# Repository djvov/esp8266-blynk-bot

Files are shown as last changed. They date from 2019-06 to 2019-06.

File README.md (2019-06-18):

# ESP8266 and BLYNK 4WD Robot

- [ESP8266 and BLYNK 4WD Robot](#esp8266-and-blynk-4wd-robot)
  * [PINOUT](#pinout)
  * [First firmware update of ESP8266](#first-firmware-update-of-esp8266)
  * [ESP8266 to breadboard](#esp8266-to-breadboard)
  * [Full Schema](#full-schema)
  * [POWER](#power)
  * [MOTOR](#motor)
  * [CONNECTION](#connection)
  * [BLYNK APP](#blynk-app)
  * [Includes](#includes)
  * [Robot settings (variable declaration)](#robot-settings)
  * [Void Setup](#void-setup)
  * [Void Loop](#void-loop)
  * [Functions](#functions)
    + [Strobo function](#strobo-function)
    + [Checkrasst function](#checkrasst-function)
    + [distanceMeasuringSonar function](#distancemeasuringsonar-function)
    + [Movement functions](#movement-functions)

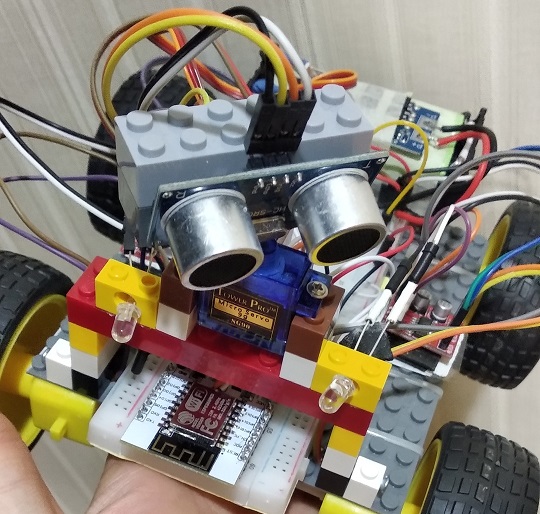
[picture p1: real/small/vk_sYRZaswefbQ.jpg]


[https://github.com/djvov/esp8266-blynk-bot/blob/master/real/vk_sYRZaswefbQ.jpg?raw=true]

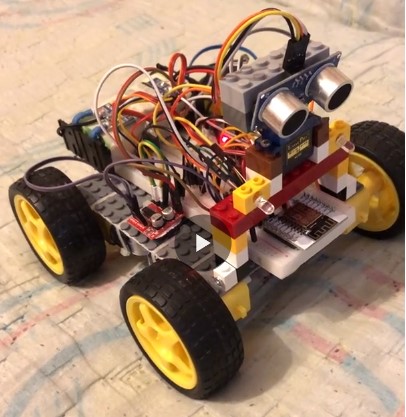
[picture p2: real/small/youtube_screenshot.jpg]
Watch the video (https://www.youtube.com/watch?v=UbAJtE57SPo)


[Table of contents](#esp8266-and-blynk-4wd-robot)

## PINOUT

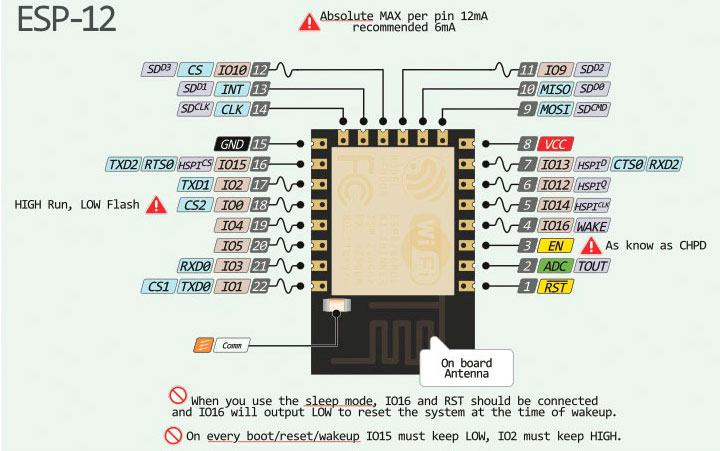
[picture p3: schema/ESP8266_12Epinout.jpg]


[Table of contents](#esp8266-and-blynk-4wd-robot)

## First firmware update of ESP8266

In Arduino IDE setup you need to put "http://arduino.esp8266.com/stable/package_esp8266com_index.json" at the line "Extend links to board manager".
Then go to the Board Manager and install ESP8266 community.
In the board menu choose your chip, my is Generic 8266.
Then your need to put esp8266 and FTDI programmator together as shown below.

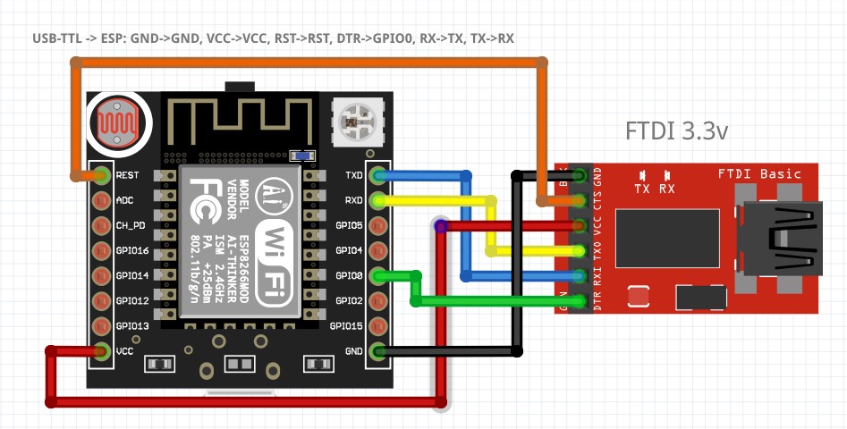
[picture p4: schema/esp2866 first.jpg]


Open Arduino OTA sketch from examples and write it.

Because in this robot I took all PINs to some tasks, we need to write firmware Over The Air. And first step is load OTA firmware to esp8266.

[Table of contents](#esp8266-and-blynk-4wd-robot)

## ESP8266 to breadboard

I'll buy native esp8266 chip and white development board.

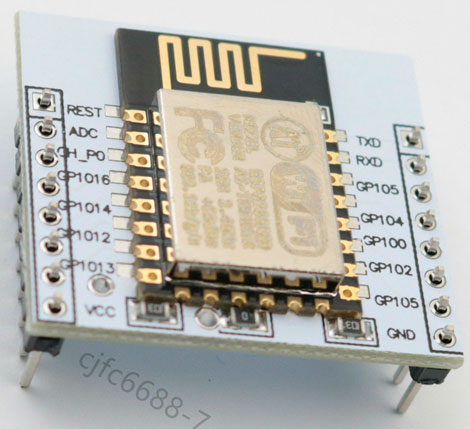
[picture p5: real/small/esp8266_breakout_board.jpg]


In the Fritzing schema I didn't find white pcb, so I put what I found, some black.
But, as white pcb, It's has some width as breadboard width. So we need to extend it by wire to another row. From 1 row to 9 row, from 2 row to 10 row, etc.

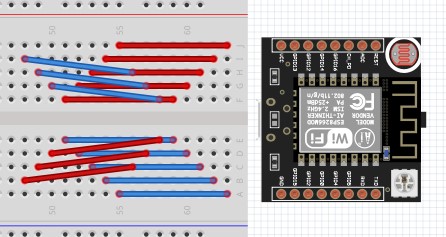
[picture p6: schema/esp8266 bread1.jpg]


The yellow lines just to show hot to each  pin goes to its row after pcb.

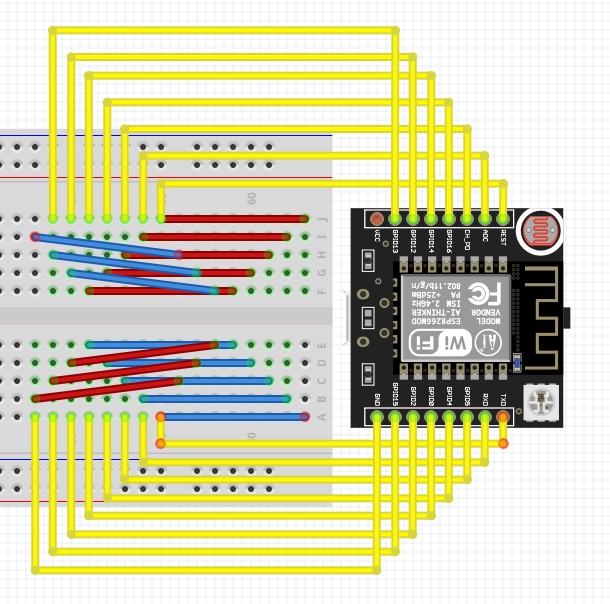
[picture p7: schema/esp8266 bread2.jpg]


[Table of contents](#esp8266-and-blynk-4wd-robot)

## Full Schema

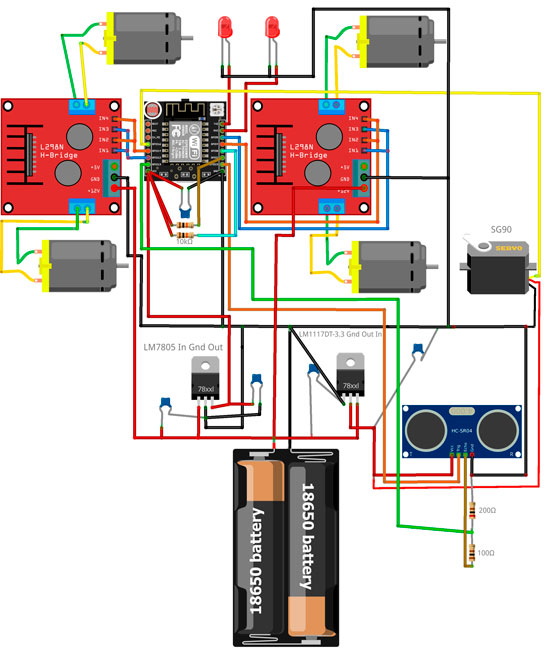
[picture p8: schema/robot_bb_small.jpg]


[https://github.com/djvov/esp8266-blynk-bot/blob/master/schema/robot_bb.jpg?raw=true]

[Table of contents](#esp8266-and-blynk-4wd-robot)

## POWER

First of all, two 18650 with serial connection to get 8.4v. With BMS plate to prevent overdischarge, and charge it with balance.
From battery block we need to build TWO special power lines: 3.3v for ESP8266, 5v for servo and HC–SR04 sonar. And raw 8.4v power for motor drivers.
3.3v we get from LM1117DT-3.3, 5v we get from LM7805. In both case two ceramic 104 capacitor for IN and OUT to ground.
**IMPORTANT!** It is necessary to connect **ALL GROUNDS**

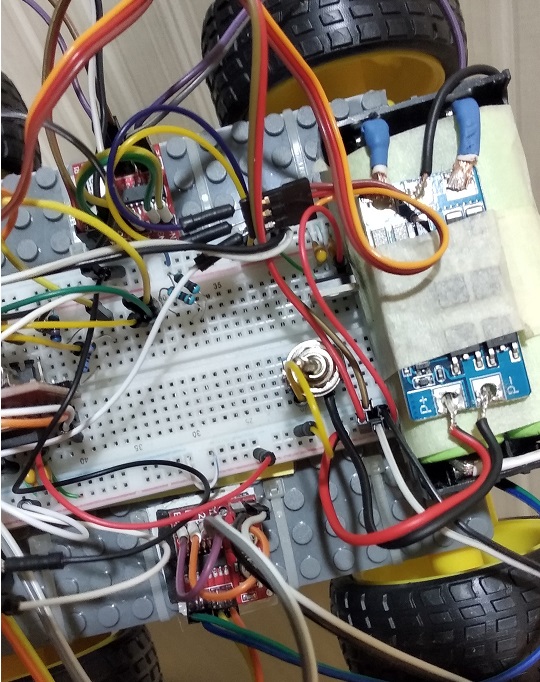
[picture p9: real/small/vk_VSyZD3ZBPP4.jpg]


[Table of contents](#esp8266-and-blynk-4wd-robot)

## MOTOR

I use MX1508 dual motors driver, analog of L298N. 1.5A per channel, 2.5A peak. With no heat sink. Becarefurl with VCC **+** and **-**.

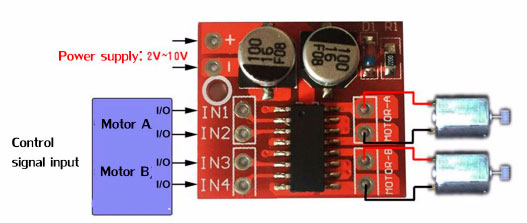
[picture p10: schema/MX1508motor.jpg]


I use two MX1508 dual motors drivers, becase  I have four wheels. One MX1508 drives two motors from same side. So we need to put IN1 and IN3 together, also IN2 and IN4, for same direction of two motors. This schema can use only two pins of ESP8266 instead of four pins.

Here is table of signal for direction, standby and brakes. Standby different from brake. Standby ends of power to motor, and motor stops by itself, it tooks some time. Brake stops motor immediately.

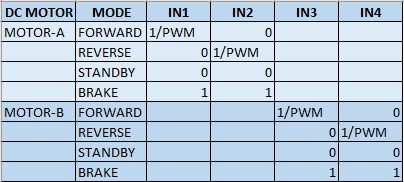
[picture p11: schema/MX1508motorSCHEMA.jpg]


[Table of contents](#esp8266-and-blynk-4wd-robot)

## CONNECTION

White board for ESP8266 already has pull-up 10k resistors for CH_PD and RESET, and pull-down 10k resistor for GPIO15. If you use native ESP8622 chip you must use put this resistor manually. Also, we has to pull-up GPIO2 and GPIO0 with 10k resistors. And I put ceramic 104 capacitor between VCC and GND of ESP8266.

```c
//motors
// left
const int in1 = 12;
const int in2 = 14;
// right
const int in3 = 5;
const int in4 = 4;
```
HC–SR04 sonar use 5v power and 5v TTL logic. But it know about 3.3v TTL for **TRIG** pin (HC–SR04 input). **BUT ECHO** pin (HC–SR04 output) needs to be connect to ESP8266 through voltage divider

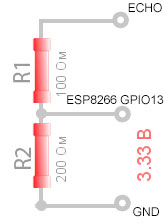
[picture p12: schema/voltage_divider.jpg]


```c
// HC–SR04 sonar
const int trigPin = 15;
const int echoPin = 13; // through voltage divider!
```
LED uses TX and RX pins. THATS WHY FIRST OF ALL WE FLSAH OTA sketch.

```c
// LED
const int led = 1;
const int led1 = 3;
```

Servo SG90 use 5v power and 5v TTL logic. But it know about 3.3v TTL for SG90 input.

```c
//servo
Servo servo1;
const int servoPin = 16;
```

[Table of contents](#esp8266-and-blynk-4wd-robot)

## BLYNK APP

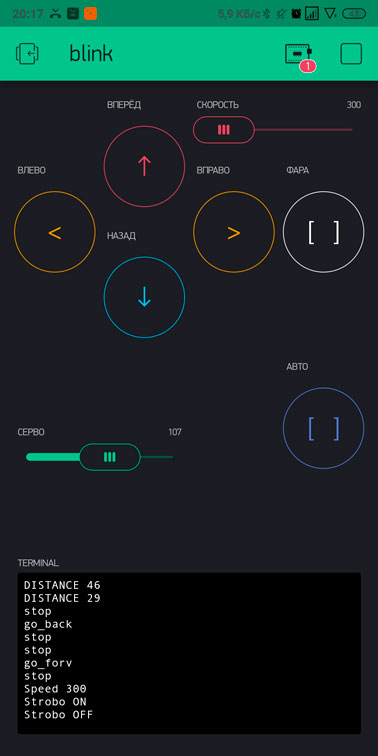
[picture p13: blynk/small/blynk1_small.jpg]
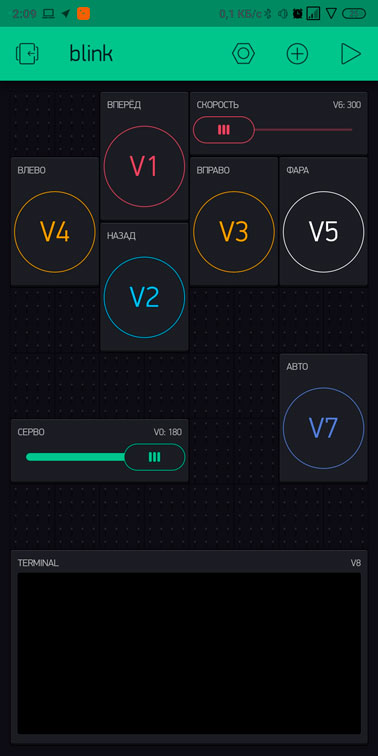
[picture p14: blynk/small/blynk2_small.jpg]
 

```
V0  slider, 0-180, decimals 0, send on release Off. Servo. Just for fun.
    In time the robot walks - servo is worked automatic.
V1-V4 push type buttons, Forward, Revers, Right, Left.
V5  switch type button. LEDs.
V6  slider, 300-600, decimals 0, send on release On. Speed.
V7  switch type button. Automatic walk.
V8  terminal
```

[Table of contents](#esp8266-and-blynk-4wd-robot)

## Includes

For use Blynk App you must need `ESP8266WiFi` and `BlynkSimpleEsp8266` libraries. `ESP8266mDNS` and `WiFiUdp` and `ArduinoOTA` for Over The Air upload. Servo for servo ;-)

```c
#include <ESP8266mDNS.h>
#include <WiFiUdp.h>
#include <ESP8266WiFi.h>
#include <BlynkSimpleEsp8266.h>
#include <ArduinoOTA.h>
#include <Servo.h>
```

[Table of contents](#esp8266-and-blynk-4wd-robot)

## Robot settings

You should get Auth Token in the Blynk App. Get it from Blynk app. And login and password to your router.

```c
// You should get Auth Token in the Blynk App.
char auth[] = "";

// Your WiFi credentials.
char ssid[] = "";
char pass[] = "";
```

Default speed. Slowest 300. If **speed < 300**, motor has not enough power to move. Fastest is 1023. But I set tup fastest is 600 because if **speed > 600**, robot could not stop before it crashes the wall ).

```c
// скорость 1023 max
int spd = 300;
// скорость автопрогулки
int autoSpd = 300;
```

`timerStrob` is for timer that runs stroboscope effect with leds.
`timerStena` is for timer that checks distance to the obstacle in manual mode, it moves the servo to which the sonar is attached.
`timerAuto` is for timer that runs auto walk, it moves the servo to which the sonar is attached.

```c
BlynkTimer timer;
int timerStrob;
int timerStena;
int timerAuto;
```

Movement flags to know where the robot is going.

```c
// флаги движения
int V1_forv = 0;
int V2_back = 0;
int V3_right = 0;
int V4_left = 0;
```

Global variable `autO` that indicates if auto walk running. Last letter is capital because `auto` is reserved word. You may name it `autoWalk`.

```c
// авто прогулка
int autO = 0;
```

Servo angles. In order for the sonar to look forward, the servo must be rotated 90 degrees. Similarly, sonar to right 50 degrees, sonar to left 140 degrees.

```c
// Углы поворота Серовпривода
int angleF = 90;
int angleR = 50;
int angleL = 140;
```

Distances in centimeters. `distAttention` - Speed higher. `distCaution` - Speed lower. `distSTOP` - STOP.

```c
// дистанции остановки
int distSTOP = 30; // дистанция СТОП!
int distCaution = 50; // дистанция ОСТОРОЖНО! скорость 300
int distAttention = 70; // дистанция ВНИМАНИЕ! скорость 400
```

Terminal widget in blynk app attached to Virtual pin 8. For some debug information.

```c
WidgetTerminal terminal(V8);
```

Delay time to stabilize servo.

```c
int delay_time = 150; // время задержки для стабилизации сервопривода
```

[Table of contents](#esp8266-and-blynk-4wd-robot)

## Void Setup

In this section you must initizlize pin mode, attach servo, move it forward (90 degrees), stop motors, turn off the leds.

```c
 // моторы
  pinMode(in1, OUTPUT);
  pinMode(in2, OUTPUT);
  pinMode(in3, OUTPUT);
  pinMode(in4, OUTPUT);
  stp(0);
  // фара leds
  pinMode(led, OUTPUT);
  pinMode(led1, OUTPUT);
  digitalWrite(led, LOW);
  digitalWrite(led1, LOW);
  //датчик расстояния sonar
  pinMode(trigPin, OUTPUT);
  pinMode(echoPin, INPUT);
  // servo
  servo1.attach(servoPin);
  servo1.write(90);
```

Timer setup. BlynkTimer is similar as SimpleTimer. First of all needs to declare timer object in global. `BlynkTimer timer;`
Timer objects can manage several timers. Each of them must be also declared. `int timerStrob;`.
Then we must determine the correspondence between variable and function.
`int setInterval(unsigned long d, timer_callback f);`
First parametr `d` is delay in milliseconds, second parameter `f` is name of callback function that runs every `d` milliseconds.

```c
  timerStrob = timer.setInterval(200, strobo);
```

And disable that timer, because we don't need to all timer functions run at startup.

```c
  timer.disable(timerStrob);
```

We do the same for all timers.

```c
  // увидел ли стену в ручном режиме
  timerStena = timer.setInterval(13L, checkrasst);
  timer.disable(timerStena);

  // автопрогулка
  timerAuto = timer.setInterval(1L, go_auto);
  timer.disable(timerAuto);
```

Then we start OTA and Blynk

```c
// по воздуху
  ArduinoOTA.begin();
  Blynk.begin(auth, ssid, pass);
```

Theb we initilize terminal widget.
`clear` function clear ther terminal. `print` and `println` functions as Serial.print, writes text and return or not return caret.
After we finished all text, we need to terminal sends data to blynk app by the `flush` function.
Lets write some 'hello' text and current IP after robot connects to router.

```c
  terminal.clear();
  terminal.println(String("Speed ") + String(spd));
  terminal.println(String("Servo 90"));
  terminal.print(String("Local IP"));
  terminal.println(WiFi.localIP());
  terminal.flush();
```

[Table of contents](#esp8266-and-blynk-4wd-robot)

## Void Loop

When you use Blynk your **loop section** must contains only `Blynk.run()`. `ArduinoOTA.handle();` if you uses OTA, and `timer.run();` if you uses timer functions. **Thats all!** All loops, cycles, events, actions, etc. in separate functions.

```c
void loop()
{
  ArduinoOTA.handle();
  Blynk.run();
  timer.run();
}
```

[Table of contents](#esp8266-and-blynk-4wd-robot)

## Functions

### Strobo function

Just blink two leds one by one.

```c
void strobo() {
  digitalWrite(led, HIGH);
  digitalWrite(led1, LOW);
  delay(100);
  digitalWrite(led, LOW);
  digitalWrite(led1, HIGH);
}
```

[Table of contents](#esp8266-and-blynk-4wd-robot)

### checkrasst function

Checks distance to the obstacle in manual mode. Servo looks forward (90 degrees). When The robot stop near the 'wall' he shakes his head like a man, means **"NO"**

```c
void checkrasst() { // проверка расстояния в ручном режиме поездки и остановка если мало
  int cm = distanceMeasuringSonar (angleF);
  if (cm<distSTOP) {
    stp(0);
    servo1.write(70);
    delay(500);
    servo1.write(110);
    delay(500);
    servo1.write(90);
  }
}
```

[Table of contents](#esp8266-and-blynk-4wd-robot)

### distanceMeasuringSonar function

Measuring distance to the obstacle at the some angle. `angle` parameter in degrees. In [settings](#robot-settings) we declare some variables for some angles. Turn the servo, wait for stabilization. Then use sonar. If result of the `pulseIn` function is **0** this means error of measurement, and we need to restart sonar by send **low** to `echoPin`, before this turn `echoPin` in **OUTPUT mode**, and back in **INPUT** mode after sonar reset. And I decided return 400cm in this case (limit of measurement). If everything is ok, divide result of the `pulseIn` function by 58, we get distance in **cm**.

```c
// *************** Функция определения Расстояния СОНАР ******************
int distanceMeasuringSonar (int angle)// функция — измерение расстояния при определенном угле поворота сервопривода
{
  int distanceSonar = 0;
  servo1.write(angle); // поворот сервопривода 1
  delay (delay_time); // подождать стабилизацию сервопривода
  digitalWrite (trigPin, LOW); // подать напряжение на сонар LOW в течении 2¦Мs
  delayMicroseconds (2);
  digitalWrite (trigPin, HIGH); // подать напряжение HIGH на сонар в течении 10¦Мs
  delayMicroseconds (10);
  digitalWrite (trigPin, LOW); // подать напряжение LOW на сонар
  int distance = pulseIn(echoPin, HIGH, 30000); // считываем данные с Сонара
  if (distance == 0)// если расстояние "0" — ошибка измерения (вне предела/завис)
  { // делаем перезагрузку сонара подачей 0 на вывод ECHO Сонара
    pinMode(echoPin, OUTPUT);
    digitalWrite(echoPin, 0);
    pinMode(echoPin, INPUT);
    // в случае ошибки измерения выводим расстояние "400 см" — расстояние вне предела измерения датчика
    distanceSonar = 400;
  } else {
    distanceSonar = distance / 58; // переводим "время" в сантиметры
  }
  terminal.print(String("DISTANCE "));
  terminal.println(distanceSonar);
  terminal.flush();
  return (distanceSonar); // возвращаем расстояние
}
```

[Table of contents](#esp8266-and-blynk-4wd-robot)

### Movement functions

All movement (forward, backward, left, right) functions excluding STOP has two parameters, delay (uses in auto walk mode), and speed.
If auto walk mode is activated, speed takes from function parameter, in manual mode speed takes from global variables spd, that regulates from blynk app by slider widget. And we enable `timerStena` in forward function when manual mode is activated. And I write in terminal what's going on.

```c
void stp(int f) { // стоп
  digitalWrite(in1, LOW);
  digitalWrite(in2, LOW);
  digitalWrite(in3, LOW);
  digitalWrite(in4, LOW);
  terminal.println(String("stop"));
  terminal.flush();
  timer.disable(timerStena);
  delay(f);
}

void go_forv(int a, int sa) {
  int spd1 = 0;
  if (autO==1) spd1=sa;
  else spd1=spd;
  if (autO==0) {
    timer.enable(timerStena);
  }
  analogWrite(in1, spd1);
  digitalWrite(in2, LOW);
  analogWrite(in3, spd1);
  digitalWrite(in4, LOW);
  terminal.println(String("go_forv"));
  terminal.flush();
  if (autO==1) {
    delay (a);
  }
}

void go_back(int g, int sg) {
  int spd1 = 0;
  if (autO==1) spd1=sg;
  else spd1=spd;
  digitalWrite(in1, LOW);
  analogWrite(in2, spd1);
  digitalWrite(in3, LOW);
  analogWrite(in4, spd1);
  terminal.println(String("go_back"));
  terminal.flush();
  if (autO==1) {
    delay (g);
  }
}

void go_left(int e, int se) {
  int spd1 = 0;
  if (autO==1) spd1=se;
  else spd1=spd;
  digitalWrite(in1, LOW);
  analogWrite(in2, spd1);
  analogWrite(in3, spd1);
  digitalWrite(in4, LOW);
  terminal.println(String("go_left"));
  terminal.flush();
  if (autO==1) {
    delay (e);
  }
}

void go_right(int d, int sd) {
  int spd1 = 0;
  if (autO==1) spd1=sd;
  else spd1=spd;
  analogWrite(in1, spd1);
  digitalWrite(in2, LOW);
  digitalWrite(in3, LOW);
  analogWrite(in4, spd1);
  terminal.println(String("go_right"));
  terminal.flush();
  if (autO==1) {
    delay (d);
  }
}
```

[Table of contents](#esp8266-and-blynk-4wd-robot)

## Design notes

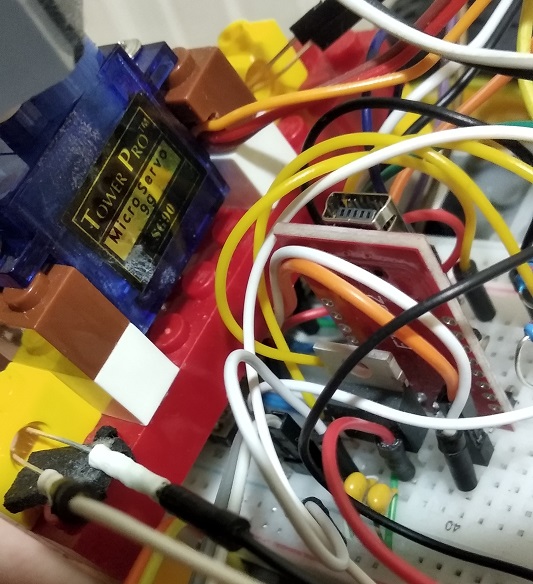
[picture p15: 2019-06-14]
real/small/vk_8p8-y3WuLLc.jpg

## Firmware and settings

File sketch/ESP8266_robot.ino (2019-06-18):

/*************************************************************
  Download latest Blynk library here:
    https://github.com/blynkkk/blynk-library/releases/latest

  Blynk is a platform with iOS and Android apps to control
  Arduino, Raspberry Pi and the likes over the Internet.
  You can easily build graphic interfaces for all your
  projects by simply dragging and dropping widgets.

    Downloads, docs, tutorials: http://www.blynk.cc
    Sketch generator:           http://examples.blynk.cc
    Blynk community:            http://community.blynk.cc
    Follow us:                  http://www.fb.com/blynkapp
                                http://twitter.com/blynk_app

  Blynk library is licensed under MIT license
  This example code is in public domain.

 *************************************************************
  This example runs directly on ESP8266 chip.

  Note: This requires ESP8266 support package:
    https://github.com/esp8266/Arduino

  Please be sure to select the right ESP8266 module
  in the Tools -> Board menu!

  Change WiFi ssid, pass, and Blynk auth token to run :)
  Feel free to apply it to any other example. It's simple!
 *************************************************************/

/* Comment this out to disable prints and save space */
// #define BLYNK_PRINT Serial
#include <ESP8266WiFi.h>

#include <ESP8266mDNS.h>
#include <WiFiUdp.h>
#include <ArduinoOTA.h>

#include <BlynkSimpleEsp8266.h>
#include <Servo.h>


// You should get Auth Token in the Blynk App.
char auth[] = "";

// Your WiFi credentials.
char ssid[] = "";
char pass[] = "";

// использованные пины 1 3 5 4 15      13 12 14 16

// моторы
const int in1 = 12;
const int in2 = 14;

const int in3 = 5;
const int in4 = 4;

// скорость 1023 max
int spd = 300;

// датчик расстояние
const int trigPin = 15;
const int echoPin = 13; // через делитель!

// фара
const int led = 3;
const int led1 = 1;
int timerStrob;

// флаги движения
int V1_forv = 0;
int V2_back = 0;
int V3_right = 0;
int V4_left = 0;

// авто прогулка
int autO = 0;

// для автопрогулки

// Углы поворота Серовпривода
int angleF = 90;
int angleR = 50;
int angleL = 140;
// дистанции остановки
int distSTOP = 30; // дистанция СТОП!
int distCaution = 50; // дистанция ОСТОРОЖНО! скорость 300
int distAttention = 70; // дистанция ВНИМАНИЕ! скорость 400

int delay_time = 150; // время задержки для стабилизации сервопривода
// скорость автопргулки
int autoSpd = 300;

BlynkTimer timer;
//таймер запуска датчика расстояния
int timerStena;
//таймер автопрогулки
int timerAuto;

//servo
const int servoPin = 16;
Servo servo1;

WidgetTerminal terminal(V8);

void strobo() {
  digitalWrite(led, HIGH);
  digitalWrite(led1, LOW);
  delay(100);
  digitalWrite(led, LOW);
  digitalWrite(led1, HIGH);
}

void stp(int f) { // стоп
  digitalWrite(in1, LOW);
  digitalWrite(in2, LOW);
  digitalWrite(in3, LOW);
  digitalWrite(in4, LOW);
  terminal.println(String("stop"));
  terminal.flush();
  timer.disable(timerStena);
  delay(f);
}

void checkrasst() { // проверка расстояния в ручном режиме поездки и остановка если мало
  int cm = distanceMeasuringSonar (angleF);
  if (cm<distSTOP) {
    stp(0);
    servo1.write(70);
    delay(500);
    servo1.write(110);
    delay(500);
    servo1.write(90);
  }
}

void go_forv(int a, int sa) {
  int spd1 = 0;
  if (autO==1) spd1=sa;
  else spd1=spd;
  if (autO==0) {
    timer.enable(timerStena);
  }
  analogWrite(in1, spd1);
  digitalWrite(in2, LOW);
  analogWrite(in3, spd1);
  digitalWrite(in4, LOW);
  terminal.println(String("go_forv"));
  terminal.flush();

  if (autO==1) {
    delay (a);
  }
}

void go_back(int g, int sg) {
  int spd1 = 0;
  if (autO==1) spd1=sg;
  else spd1=spd;
  digitalWrite(in1, LOW);
  analogWrite(in2, spd1);
  digitalWrite(in3, LOW);
  analogWrite(in4, spd1);
  terminal.println(String("go_back"));
  terminal.flush();
  if (autO==1) {
    delay (g);
  }
}

void go_left(int e, int se) {
  int spd1 = 0;
  if (autO==1) spd1=se;
  else spd1=spd;
  digitalWrite(in1, LOW);
  analogWrite(in2, spd1);
  analogWrite(in3, spd1);
  digitalWrite(in4, LOW);
  terminal.println(String("go_left"));
  terminal.flush();
  if (autO==1) {
    delay (e);
  }
}

void go_right(int d, int sd) {
  int spd1 = 0;
  if (autO==1) spd1=sd;
  else spd1=spd;
  analogWrite(in1, spd1);
  digitalWrite(in2, LOW);
  digitalWrite(in3, LOW);
  analogWrite(in4, spd1);
  terminal.println(String("go_right"));
  terminal.flush();
  if (autO==1) {
    delay (d);
  }
}

// *************** Функция определения Расстояния СОНАР ******************
int distanceMeasuringSonar (int angle)// функция — измерение расстояния при определенном угле поворота сервопривода
{
  int distanceSonar = 0;
  servo1.write(angle); // поворот сервопривода 1
  delay (delay_time); // подождать стабилизацию сервопривода
  digitalWrite (trigPin, LOW); // подать напряжение на сонар LOW в течении 2¦Мs
  delayMicroseconds (2);
  digitalWrite (trigPin, HIGH); // подать напряжение HIGH на сонар в течении 10¦Мs
  delayMicroseconds (10);
  digitalWrite (trigPin, LOW); // подать напряжение LOW на сонар
  int distance = pulseIn(echoPin, HIGH, 30000); // считываем данные с Сонара
  if (distance == 0)// если расстояние "0" — ошибка измерения (вне предела/завис)
  { // делаем перезагрузку сонара подачей 0 на вывод ECHO Сонара
    pinMode(echoPin, OUTPUT);
    digitalWrite(echoPin, 0);
    pinMode(echoPin, INPUT);
    // в случае ошибки измерения выводим расстояние "400 см" — расстояние вне предела измерения датчика
    distanceSonar = 400;
  } else {
    distanceSonar = distance / 58; // переводим "время" в сантиметры
  }
  terminal.print(String("DISTANCE "));
  terminal.println(distanceSonar);
  terminal.flush();
  return (distanceSonar); // возвращаем расстояние
}


void go_auto() {
  int distanceSonarSON_F = 0; // дистанция СОНАР впереди
  int distanceSonarSON_R = 0; // дистанция СОНАР справа
  int distanceSonarSON_L = 0; // дистанция СОНАР слева

  if (autO==1){
    distanceSonarSON_F = distanceMeasuringSonar (angleF); // запускаем функцию измерения расстояния сонаром

    // логика — если растояние меньше СТОП!
    if (distanceSonarSON_F < distSTOP) // если расстояние впереди меньше distSTOP — двигаемся назад с разворотом // stop back
    {
      stp(50); // стоп
      go_back(100, autoSpd); // двигаться назад (время, скорость)
      go_left(50, autoSpd); // поворот (время, скорость)
    }
    // логика — если растояние больше ОСТОРОЖНО
    if (distanceSonarSON_F > distCaution && distAttention > distanceSonarSON_F) // если расстояние впереди больше distCaution но меньше distAttention — двигаться ВПЕРЕД с низкой скоростьюю // forv low
    {
      go_forv (20, autoSpd); // normal Forward (время, скорость)
    }
    // логика — если растояние больше ВНИМАНИЕ
    if (distanceSonarSON_F > distAttention) // если расстояние впереди больше distAttention — двигаться ВПЕРЕД с высокой скоростью // forv high
    {
      go_forv (50, 400); // normal Forward (время, скорость)
    }

    // измеряем расстояние СПРАВА
    distanceSonarSON_R = distanceMeasuringSonar (angleR); // запускаем функцию измерения расстояния сонаром

    if (distanceSonarSON_R < distCaution) // если расстояние впереди меньше
    {
      go_left (60, autoSpd); // поворот (время, скорость)
    }

    // измеряем расстояние ПРЯМО
    distanceSonarSON_F = distanceMeasuringSonar (angleF); // запускаем функцию измерения расстояния сонаром

    // логика — если растояние меньше СТОП!
    if (distanceSonarSON_F < distSTOP) // если расстояние впереди меньше distSTOP — двигаемся назад с разворотом
    {
      stp (50); // стоп
      go_back (100, autoSpd); // двигаться назад (время, скорость)
      go_left (20, autoSpd); // поворот (время, скорость)
    }
    // логика — если растояние больше ОСТОРОЖНО
    if (distanceSonarSON_F > distCaution && distAttention > distanceSonarSON_F) // если расстояние впереди больше distCaution но меньше distAttention — двигаться ВПЕРЕД с низкой скоростью
    {
      go_forv (20, autoSpd); // normal Forward (время, скорость)
    }
    // логика — если растояние больше ВНИМАНИЕ
    if (distanceSonarSON_F > distAttention) // если расстояние впереди больше distAttention — двигаться ВПЕРЕД с высокой скоростью
    {
      go_forv (50, 400); // normal Forward (время, скорость)
    }
    // измеряем расстояние СЛЕВА
    distanceSonarSON_L = distanceMeasuringSonar (angleL); // запускаем функцию измерения расстояния сонаром
    if (distanceSonarSON_L < distCaution) // если расстояние впереди меньше distCaution
    {
      go_left (50, autoSpd); // поворот (время, скорость)
    }
  } else {
    stp(0);
  }
}

BLYNK_WRITE(V5) // ручной режим зажечь фару
{
  int snd = param.asInt(); // assigning incoming value from pin V5 to a variable
  if (snd == 1) {
    timer.enable(timerStrob);
    terminal.println(String("Strobo ON"));
    terminal.flush();
  } else {
    timer.disable(timerStrob);
    terminal.println(String("Strobo OFF"));
    terminal.flush();
    digitalWrite(led, LOW);
    digitalWrite(led1, LOW);
  }
}

BLYNK_WRITE(V0)
{
  int srv = param.asInt(); // ручной режим покрутить головой
  terminal.println(String("Servo ") + String(srv));
  terminal.flush();
  servo1.write(srv);
}

BLYNK_WRITE(V7)
{
  autO = param.asInt(); // авто прогулка
  if (autO==1) {
    timer.enable(timerAuto);
    timer.enable(timerStrob);
    terminal.println(String("AUTO ON"));
    terminal.flush();
  } else {
    stp(0);
    terminal.println(String("AUTO OFF"));
    terminal.flush();
    timer.disable(timerAuto);
    timer.disable(timerStrob);
    digitalWrite(led, LOW);
    digitalWrite(led1, LOW);
  }

}

BLYNK_WRITE(V6)
{
  spd = param.asInt(); // ручной режим установка скорости
  terminal.println(String("Speed ") + String(spd));
  terminal.flush();
}

BLYNK_WRITE(V1)
{
  V1_forv = param.asInt(); // ручной режим вперед
  if (V1_forv == 1) {
    go_forv(0,spd);
  }
  if (V1_forv == 0 && V2_back == 0 && V4_left == 0 && V3_right==0) {
    stp(0);
  }
}

BLYNK_WRITE(V2)
{
  V2_back = param.asInt(); // ручной режим назад
  if (V2_back == 1) {
    go_back(0,spd);
  }
  if (V1_forv == 0 && V2_back == 0 && V4_left == 0 && V3_right==0) {
    stp(0);
  }
}

BLYNK_WRITE(V4) // ручной режим влево
{
  V4_left = param.asInt(); // assigning incoming value from pin V4 to a variable
  if (V4_left == 1) {
    go_left(0,spd);
  }
  if (V1_forv == 0 && V2_back == 0 && V4_left == 0 && V3_right==0) {
    stp(0);
  }
}

BLYNK_WRITE(V3) // ручной режим вправо
{
  V3_right = param.asInt();
  if (V3_right == 1) {
    go_right(0,spd);
  }
  if (V1_forv == 0 && V2_back == 0 && V4_left == 0 && V3_right==0) {
    stp(0);
  }
}

void setup()
{
  // моторы
  pinMode(in1, OUTPUT);
  pinMode(in2, OUTPUT);
  pinMode(in3, OUTPUT);
  pinMode(in4, OUTPUT);
  stp(0);

  // фара
  pinMode(led, OUTPUT);
  pinMode(led1, OUTPUT);
  digitalWrite(led, LOW);
  digitalWrite(led1, LOW);

  //датчик расстояния
  pinMode(trigPin, OUTPUT);
  pinMode(echoPin, INPUT);

  // увидел ли стену в ручном режиме
  timerStena = timer.setInterval(13L, checkrasst);
  timer.disable(timerStena);

  // автопрогулка
  timerAuto = timer.setInterval(1L, go_auto);
  timer.disable(timerAuto);

  timerStrob = timer.setInterval(200L, strobo);
  timer.disable(timerStrob);

  // задаем серву
  servo1.attach(servoPin);
  servo1.write(90);
  // по воздуху
  ArduinoOTA.begin();
  Blynk.begin(auth, ssid, pass);

  terminal.clear();
  terminal.println(String("Speed ") + String(spd));
  terminal.println(String("Servo 90"));
  terminal.print(String("Local IP"));
  terminal.println(WiFi.localIP());
  terminal.flush();
}

void loop()
{
  ArduinoOTA.handle();
  Blynk.run();
  timer.run();
}
